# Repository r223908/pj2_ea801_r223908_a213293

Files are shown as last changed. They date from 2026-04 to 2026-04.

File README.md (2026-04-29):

### EA801 - PROJETO 2

### Câmbio CVT Físico com BitDogLab V7

**Autores:** 
- Raul Galdino Tancredo (RA: 223908 / [@r223908](https://github.com/r223908))
- Arthur Lucas Da Silva Nogueira (RA: 213293 / [@arthurnog](https://github.com/arthurnog)))

**Professor:** Eric Rohmer

* **Proposta de Projeto**: [Proposta em G-Docs](https://docs.google.com/document/d/18PMYSmtTR0OQQLU4SV4fV71K-Bi9EbMdW6YyoQtnZmc/edit?usp=sharing) (acesso "Comentador" para UNICAMP)
* **Relatório de projeto**: [Relatório em G-Docs](https://docs.google.com/document/d/1z_JGgpvWlYswWX_sQGRnS61v9bXmHXGZWmitXccoX50/edit?usp=sharing) (acesso "Comentador" para UNICAMP)
* **Demonstração do projeto no YouTube**: [Vídeo](https://youtu.be/2NB8YhYpBq8)

---
## ⚙️ DESCRIÇÃO DO SISTEMA (v1)
O sistema desenvolvido consiste na implementação de uma bancada de testes para um **Câmbio de Transmissão Continuamente Variável (CVT)** simulado, controlado remotamente via interface sem fio. O projeto utiliza a plataforma BitDogLab V7 como unidade central de processamento, integrando comunicação serial, controle de potência e telemetria.

O controle é dividido em dois eixos de atuação:
1. Eixo motor: Um motor de corrente contínua (DC), simulando a rotação do motor primário, controlado via PWM mas com a rotação travada em 100%.
2. Atuador do câmbio: Um segundo motor acoplado a um sistema de fuso (atuador linear), responsável por alterar a posição física da correia do câmbio CVT.

A interface homem-máquina (IHM) é realizada de forma remota através de um módulo Bluetooth (conectado à interface UART da placa) com a integração de um aplicativo no celular. O display OLED da placa é utilizado para exibir a telemetria em tempo real.

<figure align="center">
    <figcaption><i>Figura 1: Diagrama de blocos do projeto.</i></figcaption>
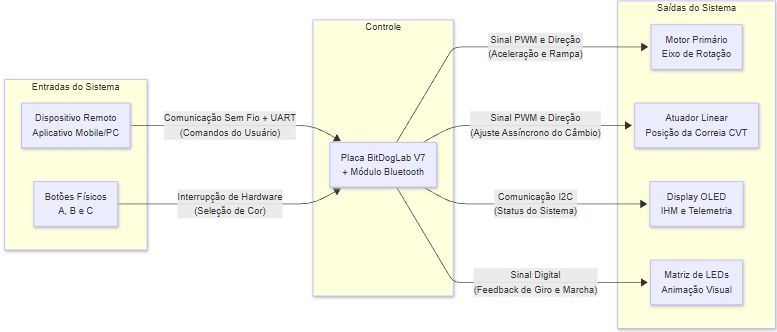
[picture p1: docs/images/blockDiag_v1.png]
Diagrama de blocos do projeto
    
    </br>
</figure>

<figure align="center">
    <figcaption><i>Figura 2: Referência de projeto feito em LEGO.</i></figcaption>
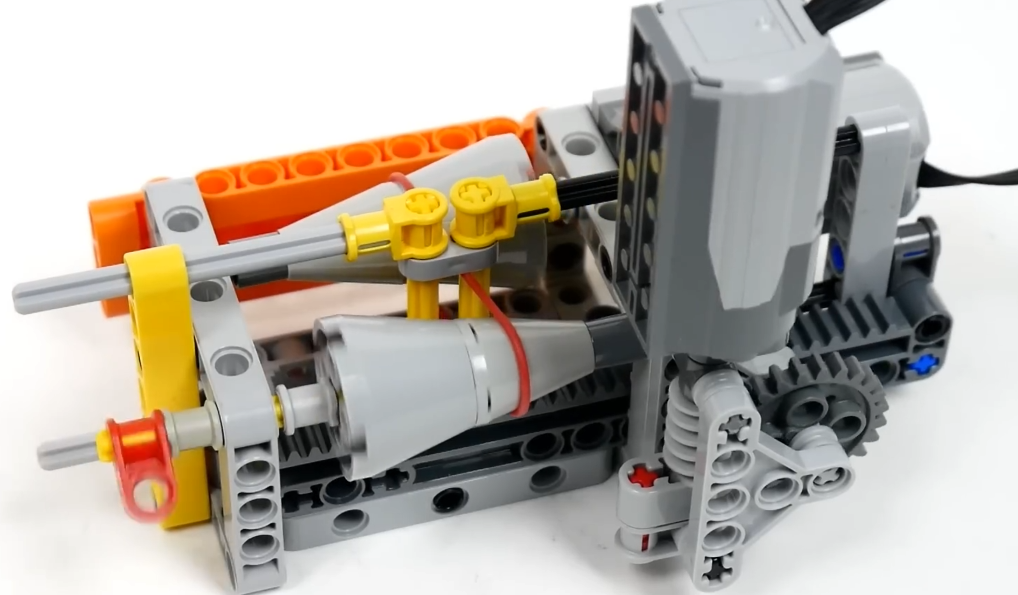
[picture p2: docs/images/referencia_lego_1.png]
Referência LEGO
    
</figure>

<figure align="center">
    <figcaption><i>Figura 3: Projeto em CAD 3D.</i></figcaption>
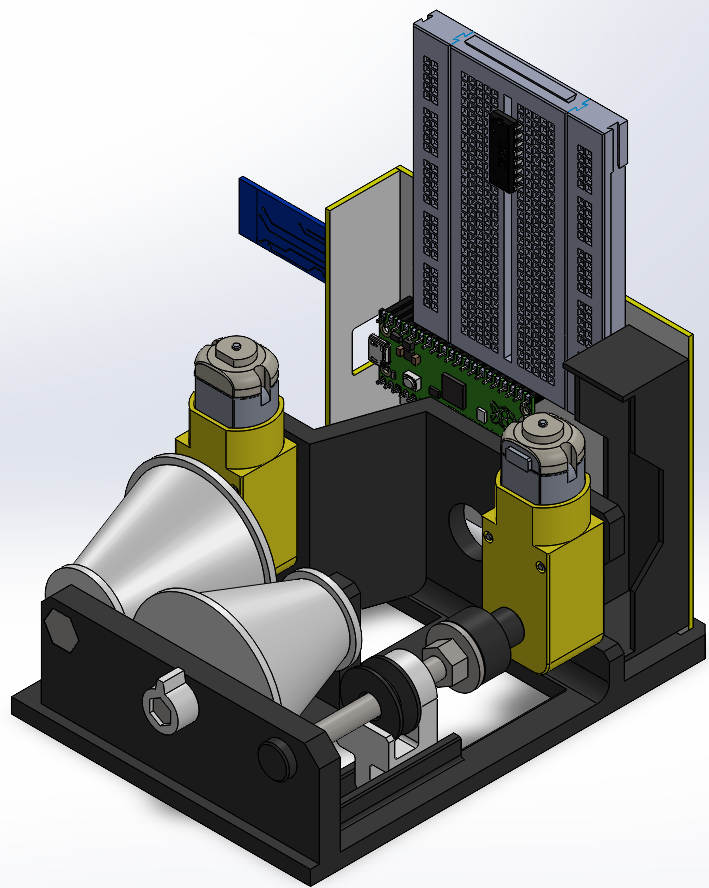
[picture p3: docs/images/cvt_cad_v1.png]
    
</figure>

<figure align="center">
    <figcaption><i>Figura 4: Equipamento testado e montado.</i></figcaption>
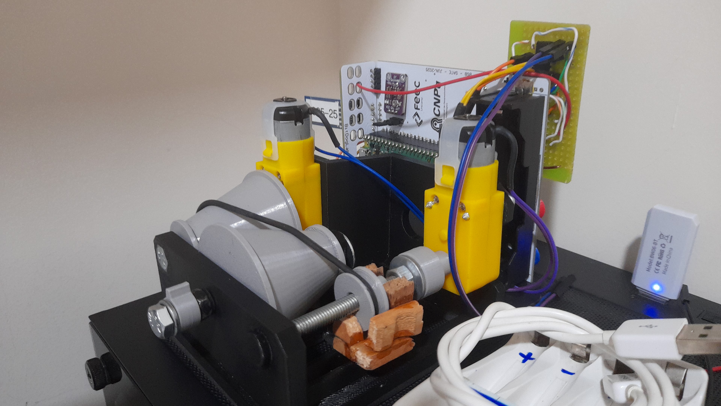
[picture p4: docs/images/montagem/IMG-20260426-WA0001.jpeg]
    
</figure>

---
## ❗REQUISITOS
- 1x BitDogLab V7.
- 2x Ponte H L293D (CI) para ambos os motores.
- 1x Protoboard 400 pinos ou fazer toda a ligação na placa de fenolite com solda.
- Jumpers M-M e M-F.
- 1x Adaptador de 4 pilhas AA (6 Vcc para os motores e alimentação da placa).
- 4x pilhas AA (1,5 Vcc).
- Cabo micro USB (usar apenas para passar a programação, com as pilhas desconectadas).
- Módulo Bluetooth HC05.
- Anel o-ring ou elástico.
- Parafusos para montagem (alguns precisam ser colados na base)
    - 2x Parafuso ISO 4017 M4x20 (Eixos do cone de saída)
    - 1x Parafuso ISO 4017 M6x15 (Contra-eixo do cone principal)
    - 1x Parafuso ISO 4017 M6x60 (fuso do CVT)
    - 2x Porca ISO 4032 M6 (Espaçador no fuso do CVT e guia da polia)
    - 1x Arruela ISO 7093 Ø6 (Espaçador no fuso do CVT)
    - 4x Parafuso autoatarrachante 9/64"x1" (ou 1/8"x1" - Ø x Comprimento)
- Peças impressas em 3D
- Ambiente de desenvolvimento configurado para MicroPython.

---
## 🔧CONFIGURAÇÕES
- BitDogLab V7: Transferir os arquivos **main.py**, **setup.py** e **ssd1306.py** para a placa via USB.
- Ligação das pontes H e motores conforme **/docs/images/schematic.png**
- Módulo Bluetooth HC05 configurado em AT Mode usando **hc05_atMode_config.py**

---
## 📚 REFERÊNCIAS
1. Repositório BitDogLab V7: [Repositório no GitHub](https://gitlab.unicamp.br/fabiano/bitdoglab-v7)
2. Banco de Informação de Hardware: [BitDogLabV7_BIH](https://docs.google.com/document/d/13-68OqiU7ISE8U2KPRUXT2ISeBl3WPhXjGDFH52eWlU/edit?tab=t.0)
3. LEGO Continuous Variable Transmission (CVT) V3 [Link YouTube](https://www.youtube.com/watch?v=sa60egMprYc)
4. LEGO Simple CVT (Continuously Variable Transmission) [Link YouTube](https://www.youtube.com/watch?v=1y5fQr0dDVg)

---
## 📄LICENÇA
* Ver o arquivo `LICENSE`.

---
## 📂 ESTRUTURA DO PROJETO
``` text
├── .vscode/                        → Listagens das config. e bibliotecas
├── docs/                           → Documentação do projeto
│   ├── CAD_files/                  → Arquivos .stl e PDF_3D da montagem
│   ├── datasheets/                 → Folhas de dados dos equipamentos utilizados
│   ├── images/                     → Imagens para relatórios e referências
│   ├── kicad_project/              → Projeto KiCad para a plaquinha shield
│   ├── mermaid_files/              → arquivos para gerar os diagramas de bloco e gantt
│   ├── video/                      → Vídeo original
│   └── (...)                       → Proposta e relatório
├── libs/                           
│   └── (...)                       → Bibliotecas e arquivos de configuração
├── src/                            
│   └── main.py                     → Código-fonte
├── .micropico                      → Arquivo necessário para a extensão Pi PICO no VSCODE
├── LICENSE                         → Licença de uso do código
└── README.md                       → Resumo e estrutura do projeto
```

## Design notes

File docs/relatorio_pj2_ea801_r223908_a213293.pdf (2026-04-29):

## UNICAMP - Universidade Estadual de Campinas

### FEEC - Faculdade de Engenharia Elétrica e de Computação

Câmbio CVT Físico com BitDogLab V7 RELATÓRIO DE PROJETO

Link deste documento (acesso Comentador para UNICAMP): Link (https://docs.google.com/document/d/1z_JGgpvWlYswWX_sQGRnS61v9bXmHXGZWmitXccoX50/edit?usp=sharing) Repositório no GitHub (https://github.com/r223908/pj2_ea801_r223908_a213293)
Vídeo de demonstração (https://youtu.be/2NB8YhYpBq8)
Arthur Lucas Da Silva Nogueira | RA: 213293
Raul Galdino Tancredo | RA: 223908

Prof. Eric Rohmer

Campinas
2026

### 1. Descrição do Sistema

O sistema desenvolvido consiste na implementação de um Câmbio de Transmissão Continuamente Variável (CVT) simulado e controlado remotamente via interface sem fio. O projeto utiliza a plataforma BitDogLab V7 como unidade central de processamento, integrando comunicação serial, controle de potência e telemetria. Utilizando uma ponte H L293D, o controle dos motores é dividido em dois eixos de atuação:
1. Eixo motor: motor de corrente contínua (DC) responsável pela força motriz principal, conectado ao cone principal.
2. Atuador do câmbio: motor de corrente contínua acoplado a um sistema de fuso (atuador linear), responsável por alterar a posição física da correia do câmbio CVT. No sistema de fuso, há a polia (que tem o anel o-ring/elástico girando livremente) e a guia, que faz com que o movimento de rotação do fuso se transforme em movimento linear.

A interface homem-máquina (IHM) é realizada de forma remota através de um módulo Bluetooth (conectado à interface UART da placa) com a integração de um aplicativo no celular (“Arduino Bluetooth Control” na Play Store do Google). O display OLED da placa é utilizado para exibir a telemetria em tempo real.

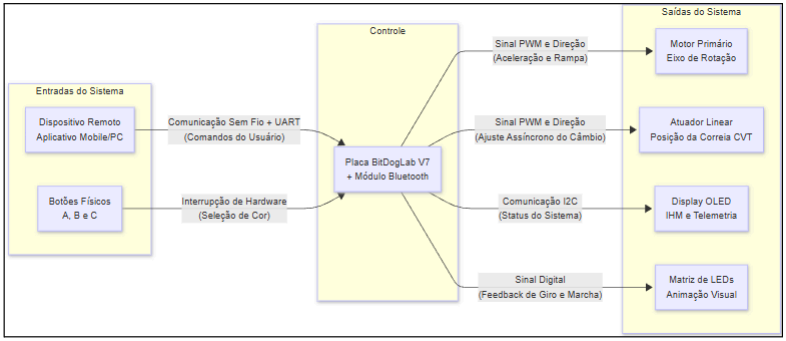
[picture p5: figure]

Figura 1 - Arquitetura do sistema.

Python

### 2. Código fonte

- Configuração do módulo Bluetooth HC-05: /libs/hc05_atMode_config.py (https://github.com/r223908/pj2_ea801_r223908_a213293/blob/main/libs/hc05_atMode_config.py)

"""
Como usar:
1. Segurar botão da placa HC-05 (ao ligar a BitDogLab, o módulo vai piscar os LEDs a cada 2 segundos).
2. Inserir o cabo USB na entrada da BitDogLab.
3. No VSCode, selecionar este .py na árvore usar a opção "Run current file on Pico"
4. Testar interface com o comando "AT" --> Deve aparecer um "OK" onde estava o "AT".
5. Configurar usuário da placa:
a. AT+NAME=.... | --> digitar o nome do módulo; e.g.: AT+NAME=EA801_CVT
b. AT+PSWD=xxxx | --> senha de 4 digitos = xxxx
c. AT+CMODE=1 | --> para se conectar com qualquer dispositivo através da
senha
6. Desligar a placa e realizar pareamento.
A. Para mais comandos, ver /docs/datasheets/HC-05_ATCommandSet.pdf """

import machine
import sys
import uselect
import utime

# Configura a UART0 nos pinos 0 (TX) e 1 (RX) - Conector J2

# O baud rate de 38400 é o padrão de fábrica para o modo AT do HC-05

uart = machine.UART(0, baudrate=38400, tx=machine.Pin(0), rx=machine.Pin(1))

print("==================================")
print(" | Terminal AT para HC-05 | ")
print("==================================")
print("Digite 'AT' e pressione Enter.")
print("A resposta deve ser 'OK'.") print("==================================")

# Configura a entrada do teclado (terminal USB) para não bloquear o código teclado = uselect.poll()

teclado.register(sys.stdin, uselect.POLLIN)

# Envia um "AT" inicial de teste (igual ao seu código C++)

Python

uart.write('AT\r\n')

while True:
# 1. Se chegou algo do HC-05, imprime no terminal do PC

if uart.any():
resposta = uart.read()
if resposta is not None: | # sem isso vai aparecer um erro no decode
abaixo
try:
print(resposta.decode('utf-8'), end='')
except UnicodeError:
print(resposta) # Imprime cru se houver lixo na serial

# 2. Se digitar algo no terminal do PC, 05envia para o HC-

if teclado.poll(0):
comando = sys.stdin.readline().strip() # Lê o que foi digitado
if comando:
# O HC-05 exige que os comandos AT terminem com Carriage Return e Line Feed (\r\n)

uart.write(comando + '\r\n')

utime.sleep(0.01) # Pequena pausa para não sobrecarregar o processador

- Mapeamento de comandos Bluetooth: /libs/bluetooth_mapping.py (https://github.com/r223908/pj2_ea801_r223908_a213293/blob/main/libs/bluetooth_mapping.py)

"""
1. Arquivo de uso geral para mapear o que chega de informação na UART com o módulo bluetooth.
2. Utilizado para reconhecer os comandos e configurar o setup.py deste projeto.
3. O que a placa receber será exibido no Terminal do VSCode.
"""

import machine
import utime

# Inicializa a UART0 para o Bluetooth (Pinos do Conector J2)

# Baud rate 9600 é o padrão para comunicação (modo transparente)

bluetooth = machine.UART(0, baudrate=9600, tx=machine.Pin(0), rx=machine.Pin(1))

# Configura o LED Azul da placa (GPIO 12) para feedback visual

# O BIH diz que é cátodo comum, então '1' liga e '0' desliga

led_azul = machine.Pin(12, machine.Pin.OUT)
led_azul.value(0) # Inicia desligado

Python

print("=======================================")
print(" | Monitor Bluetooth - Projeto CVT | ")
print("=======================================") print("Aguardando conexão e comandos do celular...")

while True:
# Verifica se há dados no buffer do Bluetooth if bluetooth.any():

| # Lê os dados brutos recebidos dados_brutos = bluetooth.read()
| try:
# Tenta decodificar de bytes para texto (String)

# O .strip() remove espaços em branco e quebras de linha (\r, \n) das pontas

comando = dados_brutos.decode('utf-8').strip() # type: ignore

# Só imprime se realmente tiver algo após o strip

| if comando:
print(f"Comando recebido em Texto: '{comando}'")

# Envia um "eco" de volta para o celular (aparece na tela do app) bluetooth.write(f"Placa recebeu: {comando}\n")

| # Pisca o LED Azul rapidamente led_azul.value(1) utime.sleep(0.1) led_azul.value(0)
| except UnicodeError:
# Se o aplicativo do celular mandar dados hexadecimais puros

# (comum em apps de controle tipo "joystick"), a decodificação de texto falha.

# Nesse caso, imprimimos os bytes puros para você poder mapear. print(f"Dados recebidos em Bytes (Hex): {dados_brutos}")

# Pausa curta para não travar a CPU no loop infinito utime.sleep(0.05)

- Setup do projeto: /libs/setup.py (https://github.com/r223908/pj2_ea801_r223908_a213293/blob/main/libs/setup.py)

"""
arquivo de importação de bibliotecas, configuração de interfaces e variáveis """

from machine import Pin, ADC, I2C, PWM import neopixel, utime, machine import ssd1306

# 1. Variáveis Globais e Cores corVermelha = (20, 0, 0)

corAzul = (0, 0, 20)
corVerde = (0, 20, 0)
cor_travada = corVermelha # Motor começa vermelho ultimo_tempo_btn = 0
ultimo_tempo_pisca = utime.ticks_ms() indice_frame = 0

# 2. Variáveis de Controle do Motor Virtual

CENTRO_JOYSTICK = 32768
ZONA_MORTA = 4000
MAX_LEDS_POR_SEGUNDO = 100 # Ajuste a velocidade máxima aqui

# 3. Configuração dos Botões (A, B e C)

botao_a = Pin(5, Pin.IN, Pin.PULL_UP)
botao_b = Pin(6, Pin.IN, Pin.PULL_UP)
botao_c = Pin(10, Pin.IN, Pin.PULL_UP)

# 4. Configuração do Joystick

joystick_x = ADC(Pin(27))
joystick_y = ADC(Pin(26))
joystick_sw = Pin(22, Pin.IN, Pin.PULL_UP)

# 5. Configuração do Display OLED (SSD1306)

# Usando os pinos I2C0 da BitDogLab V7 (SDA=2, SCL=3) i2c = I2C(1, scl=Pin(3), sda=Pin(2), freq=400000) display = ssd1306.SSD1306_I2C(128, 64, i2c, addr=0x3C) display.fill(0)

display.show()
ATT_DISPLAY_MS = 100

# 6. Configuração da Matriz de LEDs NUM_LEDS = 25

np = neopixel.NeoPixel(Pin(7), NUM_LEDS)
LED_MEIO = 12
# Buffer circular da animação do motor

FRAMES_MOTOR = [[14, 13], [15, 16], [16, 24], [16, 23], [17, 22], [18, 21], [18, 20], [18, 19], [10, 11], [8, 9],

[0, 8], [1, 8], [2, 7], [3, 6], [4, 6], [5, 6] ]

# 7. Configuração dos controles de Motor (Ponte H) e PWM da placa

# IMPORTANTE: GPIO 0 e 1 são do Bluetooth. Vamos usar os pinos livres do conector IDC.

# Motor Principal (Eixo)

Mprincipal_DIR1 = Pin(16, Pin.OUT)
Mprincipal_DIR2 = Pin(17, Pin.OUT) Mprincipal_PWM = PWM(Pin(18)) Mprincipal_PWM.freq(1000)
Mprincipal_PWM.duty_u16(0) TEMPO_RAMPA_MS = 1000
# Motor Câmbio (Atuador CVT) Mcambio_DIR1 = Pin(19, Pin.OUT) Mcambio_DIR2 = Pin(8, Pin.OUT) Mcambio_PWM = PWM(Pin(9))

Mcambio_PWM.freq(1000)
Mcambio_PWM.duty_u16(0)
TEMPO_PASSO_CVT_MS = 2000 # 2000 ms = 2 segundos

# 8. Configura o LED Azul da placa (GPIO 12) para feedback visual led_azul = machine.Pin(12, machine.Pin.OUT)

led_azul.value(0) # Inicia desligado

# 9. Inicializa a UART0 para o Bluetooth (Pinos do Conector J2)

bluetooth = machine.UART(0, baudrate=9600, tx=machine.Pin(0), rx=machine.Pin(1)) status_bt = machine.Pin(4, machine.Pin.IN) # Pino que vai ler o pino 'STATE' do módulo Bluetooth

# 10. Mapeamento das entradas bluetooth

outButtonDir = '0'
frontDir = 'F'
backDir = 'B'
rightDir = 'R'
leftDir = 'L'
triangleDir = 'T'
circleDir = 'C'
squareDir = 'S'
crossDir = 'X'
startDir = 'A'
pauseDir = 'P'

Python

- Arquivo principal: /src/main.py (https://github.com/r223908/pj2_ea801_r223908_a213293/blob/main/src/main.py)

from setup import *

# ========================================== # FUNÇÕES DE HARDWARE (MOTORES E TELA)

# ==========================================

# Lida com as informações do display OLED

def printOled(velocidade, direcao, posicao_cvt, bt_conectado): texto_sentido = "Horario" if direcao == 1 else "Anti-Hor." texto_sentido = "Parado" if velocidade == 0 else texto_sentido texto_bt = "ON" if bt_conectado == 1 else "OFF" display.fill(0)
display.text("Cambio CVT", 20, 0)
display.text("-" * 16, 0, 10) display.text(f"Motor: {texto_sentido}", 0, 25) display.text(f"Pos. CVT: {posicao_cvt}%", 0, 40)
display.text(f"Bluetooth: {texto_bt}", 0, 55)
display.show()

#controle do motor principal, lidando com a velocidade (mantida em 100%) e sentido de giro

def controlar_motor_principal(velocidade_percentual, direcao, fazer_rampa=False): # verificação se recebeu o comando para inverter o sentido do motor ou parar # nos dois casos tem rampa de variação de velocidade para não ter um solavanco nos componentes mecânicos
if fazer_rampa and velocidade_percentual > 0:
passos = 10
tempo_por_passo = (TEMPO_RAMPA_MS / 2000) / passos passo_pwm = max(1, velocidade_percentual // passos) for v in range(velocidade_percentual, -1, -passo_pwm): Mprincipal_PWM.duty_u16(int((v / 100) * 65535)) utime.sleep(tempo_por_passo) Mprincipal_DIR1.value(0)
Mprincipal_DIR2.value(0)
Mprincipal_PWM.duty_u16(0)
utime.sleep(0.05)
if direcao == 1: | # a mudança de direção pode ser feita na
inversão dos fios de alimentação do motor Mprincipal_DIR1.value(1)
Mprincipal_DIR2.value(0)
else:
Mprincipal_DIR1.value(0)
Mprincipal_DIR2.value(1)
for v in range(0, velocidade_percentual + 1, passo_pwm):

Mprincipal_PWM.duty_u16(int((v / 100) * 65535)) utime.sleep(tempo_por_passo) Mprincipal_PWM.duty_u16(int((velocidade_percentual / 100) * 65535))
else: | # controle normal, apenas ocorre se recebe algum comando via
Bluetooth
if velocidade_percentual > 0:
| if direcao == 1: Mprincipal_DIR1.value(1) Mprincipal_DIR2.value(0)

else:
| Mprincipal_DIR1.value(0) Mprincipal_DIR2.value(1)

else:
| Mprincipal_DIR1.value(0) Mprincipal_DIR2.value(0)

Mprincipal_PWM.duty_u16(int((velocidade_percentual / 100) * 65535))

# movimentação do câmbio, dependendo do sentido que ele precisar girar # velocidade também sempre em 100%

def iniciar_movimento_cvt(direcao):
if direcao == 1:
Mcambio_DIR1.value(1)
Mcambio_DIR2.value(0)
elif direcao == -1:
Mcambio_DIR1.value(0)
Mcambio_DIR2.value(1)
else:
return
Mcambio_PWM.duty_u16(65535)

# ========================================== # Função de Interrupção dos Botões

# ========================================== def trata_interrupcao_botao(pino):

global cor_travada, ultimo_tempo_btn
tempo_atual = utime.ticks_ms()
if utime.ticks_diff(tempo_atual, ultimo_tempo_btn) > 200: if pino == botao_a:
| cor_travada = corVermelha
elif pino == botao_b:
| cor_travada = corAzul
elif pino == botao_c:
| cor_travada = corVerde
ultimo_tempo_btn = tempo_atual botao_a.irq(trigger=Pin.IRQ_FALLING, handler=trata_interrupcao_botao) botao_b.irq(trigger=Pin.IRQ_FALLING, handler=trata_interrupcao_botao) botao_c.irq(trigger=Pin.IRQ_FALLING, handler=trata_interrupcao_botao)

# ==========================================

# INICIALIZAÇÃO E LOOP PRINCIPAL

# ==========================================

ultimo_tempo_pisca = utime.ticks_ms() ultimo_tempo_oled = utime.ticks_ms()

# inicializacao dos motores velocidade_atual = 0

direcao_motor = 1
posicao_cvt = 0

# VARIÁVEIS PARA O CVT ASSÍNCRONO cvt_em_movimento = False

ultimo_tempo_cvt = 0

# desliga a matriz de LEDs

for i in range(NUM_LEDS):
np[i] = (0, 0, 0)
np.write()

print("Aguardando comandos Bluetooth...")

while True:
tempo_atual = utime.ticks_ms()

# 1. ATUALIZAÇÃO DO DISPLAY OLED

if utime.ticks_diff(tempo_atual, ultimo_tempo_oled) >= ATT_DISPLAY_MS: estado_conexao = status_bt.value()
if estado_conexao == 0 and velocidade_atual > 0:
passos = 10
tempo_por_passo = (TEMPO_RAMPA_MS / 2000) / passos passo_pwm = max(1, velocidade_atual // passos)
for v in range(velocidade_atual, -1, -passo_pwm): Mprincipal_PWM.duty_u16(int((v / 100) * 65535)) utime.sleep(tempo_por_passo)
velocidade_atual = 0
controlar_motor_principal(0, direcao_motor) printOled(velocidade_atual, direcao_motor, posicao_cvt, estado_conexao) ultimo_tempo_oled = tempo_atual

# 2. LEITURA DE COMANDOS BLUETOOTH

if bluetooth.any():
try:
dados_brutos = bluetooth.read()
if dados_brutos is not None:
comando = dados_brutos.decode('utf-8').strip().upper()

if comando:
led_azul.value(1)
if comando == startDir: | # ligar motor principal
velocidade_atual = 100
controlar_motor_principal(velocidade_atual, direcao_motor)
elif comando == frontDir: | # sentido horário
deve_fazer_rampa = (direcao_motor == -1 and velocidade_atual > 0)
direcao_motor = 1
controlar_motor_principal(velocidade_atual, direcao_motor, deve_fazer_rampa)
elif comando == backDir: | # sentido anti-horário
deve_fazer_rampa = (direcao_motor == 1 and velocidade_atual > 0)
direcao_motor = -1
controlar_motor_principal(velocidade_atual, direcao_motor, deve_fazer_rampa)

elif comando == triangleDir: # sobe marcha; motor CVT
# Adicionada a regra: "not cvt_em_movimento" para evitar acúmulo de comandos

if posicao_cvt < 100 and not cvt_em_movimento: iniciar_movimento_cvt(1)
cvt_em_movimento = True
ultimo_tempo_cvt = tempo_atual # Marca a hora que ligou
posicao_cvt = min(100, posicao_cvt + 10)
elif comando == crossDir: | # desce marcha; motor CVT
if posicao_cvt > 0 and not cvt_em_movimento: iniciar_movimento_cvt(-1)
cvt_em_movimento = True
ultimo_tempo_cvt = tempo_atual # Marca a hora que ligou
posicao_cvt = max(0, posicao_cvt - 10)

elif comando == pauseDir: | # para o motor principal
velocidade_atual = 0
controlar_motor_principal(0, direcao_motor)
# Parada de emergência para o Câmbio também! Mcambio_DIR1.value(0)

Mcambio_DIR2.value(0)
Mcambio_PWM.duty_u16(0)
cvt_em_movimento = False

led_azul.value(0)
except UnicodeError:
pass

# 3. VERIFICADOR ASSÍNCRONO DO MOTOR CVT

# Fica verificando se o tempo do motor do câmbio já deu

if cvt_em_movimento:
if utime.ticks_diff(tempo_atual, ultimo_tempo_cvt) >= TEMPO_PASSO_CVT_MS: # O tempo do passo (ex: 2s) acabou! Desliga o motor do CVT. Mcambio_DIR1.value(0)
Mcambio_DIR2.value(0)
Mcambio_PWM.duty_u16(0)
cvt_em_movimento = False

# 4. ANIMAÇÃO DA MATRIZ DE LEDS PARA REPLICAR O SENTIDO DE GIRO DO MOTOR PRINCIPAL

np.fill((0, 0, 0))
if posicao_cvt == 0 or velocidade_atual == 0:
np[LED_MEIO] = cor_travada
else:
leds_por_segundo = (posicao_cvt / 100) * MAX_LEDS_POR_SEGUNDO leds_por_segundo = .1 if leds_por_segundo < 0.1 else leds_por_segundo intervalo_ms = int(1000 / leds_por_segundo)

if utime.ticks_diff(tempo_atual, ultimo_tempo_pisca) >= intervalo_ms: if direcao_motor == 1:
indice_frame = (indice_frame + 1) % len(FRAMES_MOTOR) else:
indice_frame = (indice_frame - 1) % len(FRAMES_MOTOR)

ultimo_tempo_pisca = tempo_atual

for led in FRAMES_MOTOR[indice_frame]: np[led] = cor_travada
np.write()

JSON

utime.sleep(0.01)

Para que a pasta /libs/ seja reconhecida ao clonar o repositório, é necessário alterar/criar o arquivo settings.json na pasta .vscode /.vscode/settings.json com a linha "./libs":

{
"python.languageServer": "Pylance", "python.analysis.typeCheckingMode": "basic", "python.analysis.diagnosticSeverityOverrides": { "reportMissingModuleSource": "none"
},
"python.terminal.activateEnvironment": false, "micropico.openOnStart": true, "python.analysis.typeshedPaths": [ "~/.micropico-stubs/included"
],
"python.analysis.extraPaths": [ "~/.micropico-stubs/included", "./libs"
]
}

### 3. Projeto CAD 3D

Com o auxílio de um software de modelagem 3D, foram criadas as peças para impressão 3D dos componentes do projeto: base, cones, polias (de saída e da guia do câmbio), guia e acoplamento do câmbio.
Com os arquivos prontos, é necessário gerar para cada uma das peças um arquivo .stl que é utilizado nas impressoras 3D. Para este projeto, os arquivos podem ser encontrados em:
- Arquivos .stl e PDF 3D: /docs/CAD_files. (https://github.com/r223908/pj2_ea801_r223908_a213293/tree/main/docs/CAD_files)

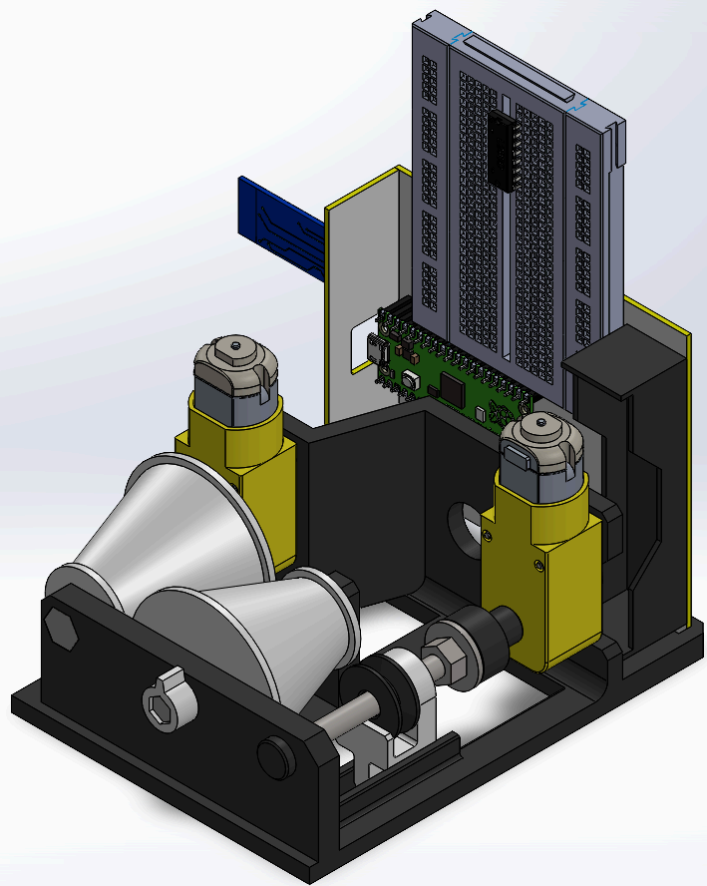
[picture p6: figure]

Figura 2 - Montagem 3D do projeto preliminar.

### 4. Montagem e desvios de projeto

Previamente à manufatura das peças em 3D, realizaram-se os testes de bancada para validar a programação e o acionamento dos motores. Após a validação de ambos os atuadores, o sistema de controle com a ponte H foi consolidado em uma placa de fenolite. O objetivo dessa montagem foi conferir estabilidade física aos componentes elétricos e mitigar o risco de rompimento dos cabos quando o sistema fosse submetido a vibrações.

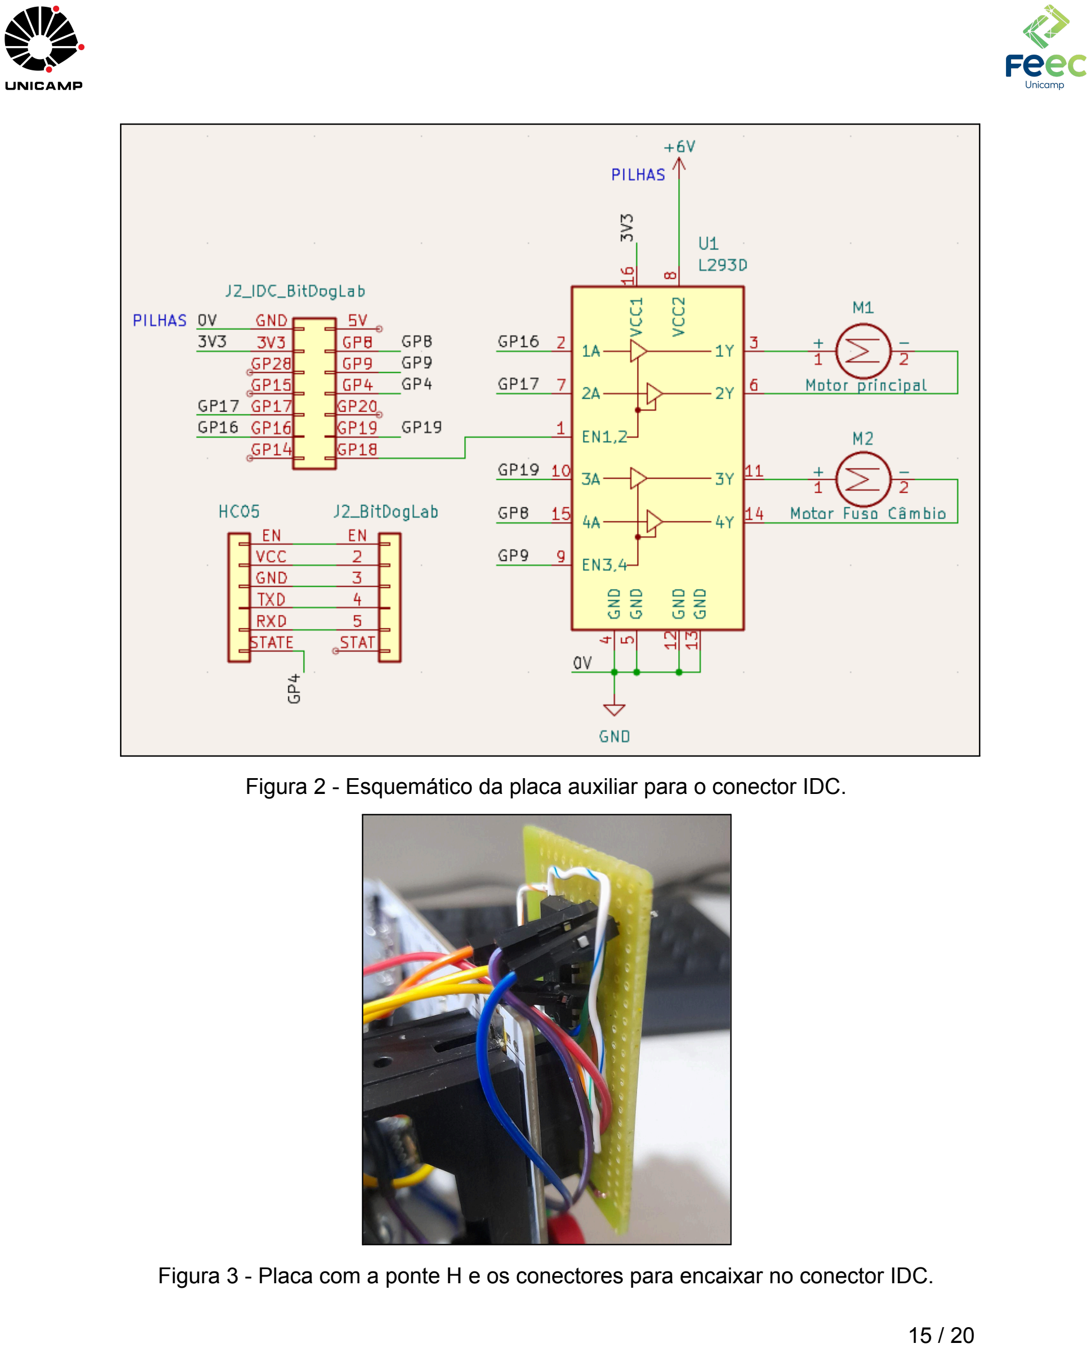
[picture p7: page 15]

Figura 2 - Esquemático da placa auxiliar para o conector IDC.

Figura 3 - Placa com a ponte H e os conectores para encaixar no conector IDC.

Foi adaptado um carregador de pilhas AA/AAA para que ele fosse utilizado como adaptador de 4 pilhas AA para 6 Vcc para alimentação dos motores. Foi feita uma tentativa de alimentação da placa com estes 6V com o auxílio de 2 diodos 1N4007 (gerando 4,6V para o pino 5V do conector IDC), mas as pilhas se provaram insuficientes para a carga da placa e dos dois motores.

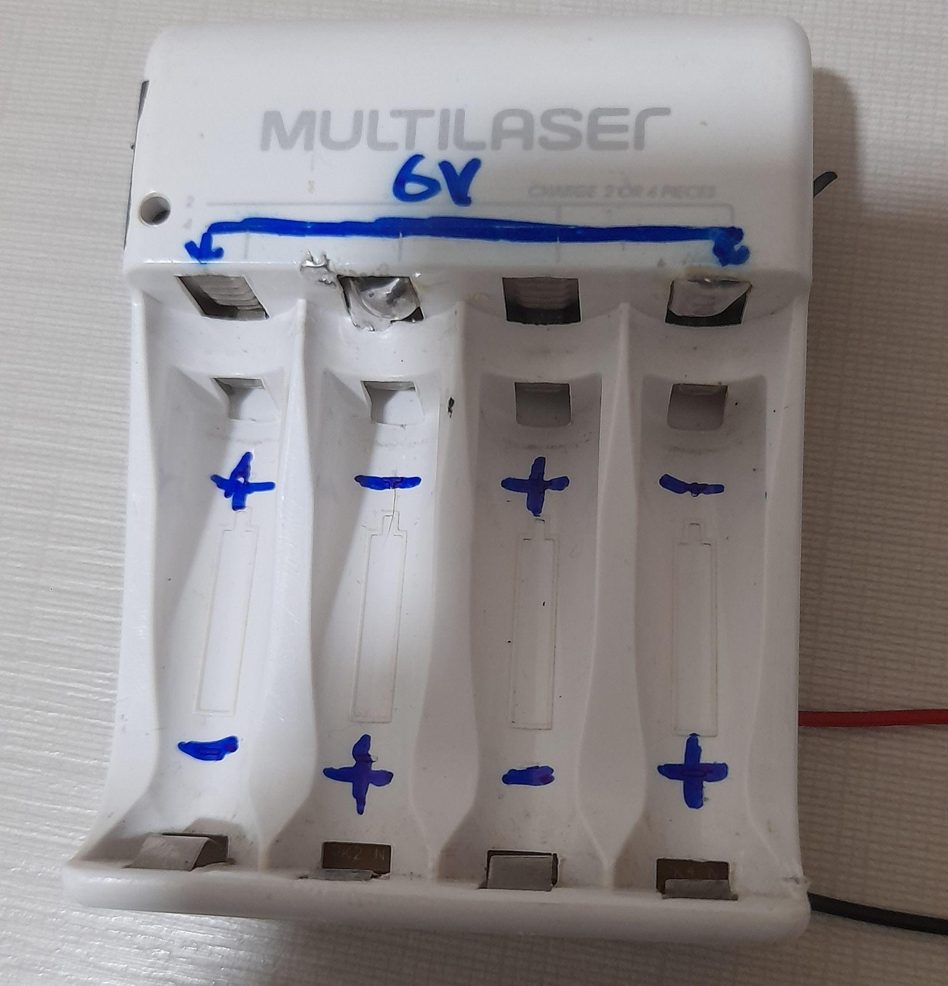
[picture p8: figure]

Figura 4 - Adaptador de pilhas AA para 6 Vcc.

Para a conexão do módulo Bluetooth, a BitDogLab conta com o jumper J2. A única alteração que precisou ser feita é em relação ao pino de estado da conexão bluetooth. Para monitorar se o sistema estava conectado ao celular ou não, foi necessário remover apenas o pino STATE do jumper J2 e colocá-lo na GP4 pois a BitDogLab não possui nenhuma conexão deste pino com alguma entrada da placa.

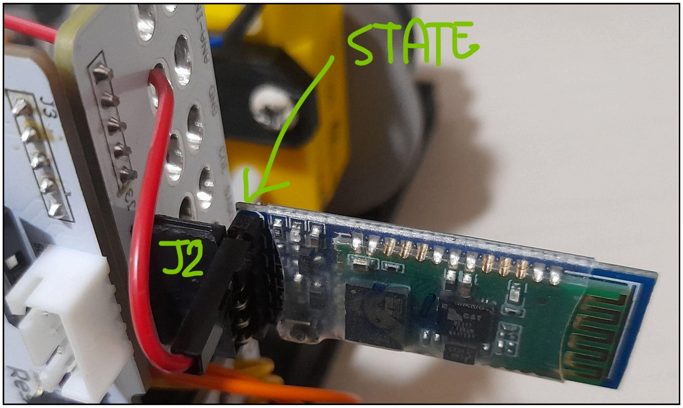
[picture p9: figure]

Figura 5 - Adaptação no módulo HC-05 e jumper J2.

Após a impressão das peças, notou-se que um dos arquivos .stl não foi enviado: a guia da polia do câmbio. Esta peça é responsável por fazer com que uma porca M6 no fuso não gire junto com sua rotação. Assim, o movimento circular realizado pelo fuso é transformado em movimento linear. Para mitigar este problema sem atrasar os testes, foi feito um suporte com prendedores de roupa.

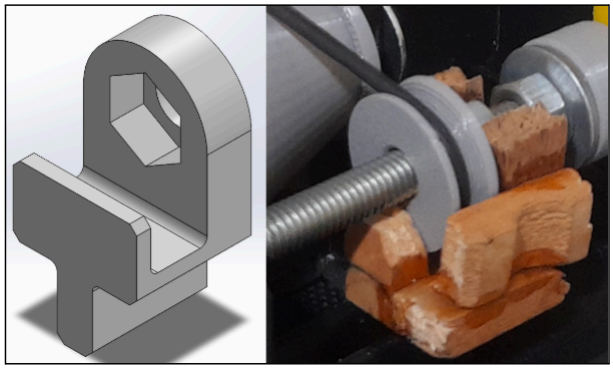
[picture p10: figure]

Figura 6 - Comparativo entre a peça projetada e a peça fabricada para os testes.

### 5. Testes realizados

Os motores foram testados individualmente antes das peças 3D ficarem prontas, validando a lógica de controle do equipamento. O mesmo é válido para a placa que substituiu a protoboard.
Com a confecção das peças em 3D e montagem do sistema, constatou-se que os cones estavam raspando na base e nos parafusos dos eixos. Com as ferramentas adequadas, a peça base foi retrabalhada e os furos centrais dos cones foram aumentados. Com estas alterações, o projeto 3D foi asbuiltado para que numa futura montagem não ocorram os mesmos problemas.
Resolvidos os problemas de interferência das peças, foram feitos alguns testes com o controle dos motores e foi encontrado apenas um problema crítico ao projeto: a guia do câmbio.
Como a guia está em uma extremidade do sistema, o anel o-ring utilizado como “correia” não fica perfeitamente reto ao longo da sua passagem pelos cones. Assim, quanto mais próximo da posição 0%, maior a divergência no tracionamento do cone de saída.

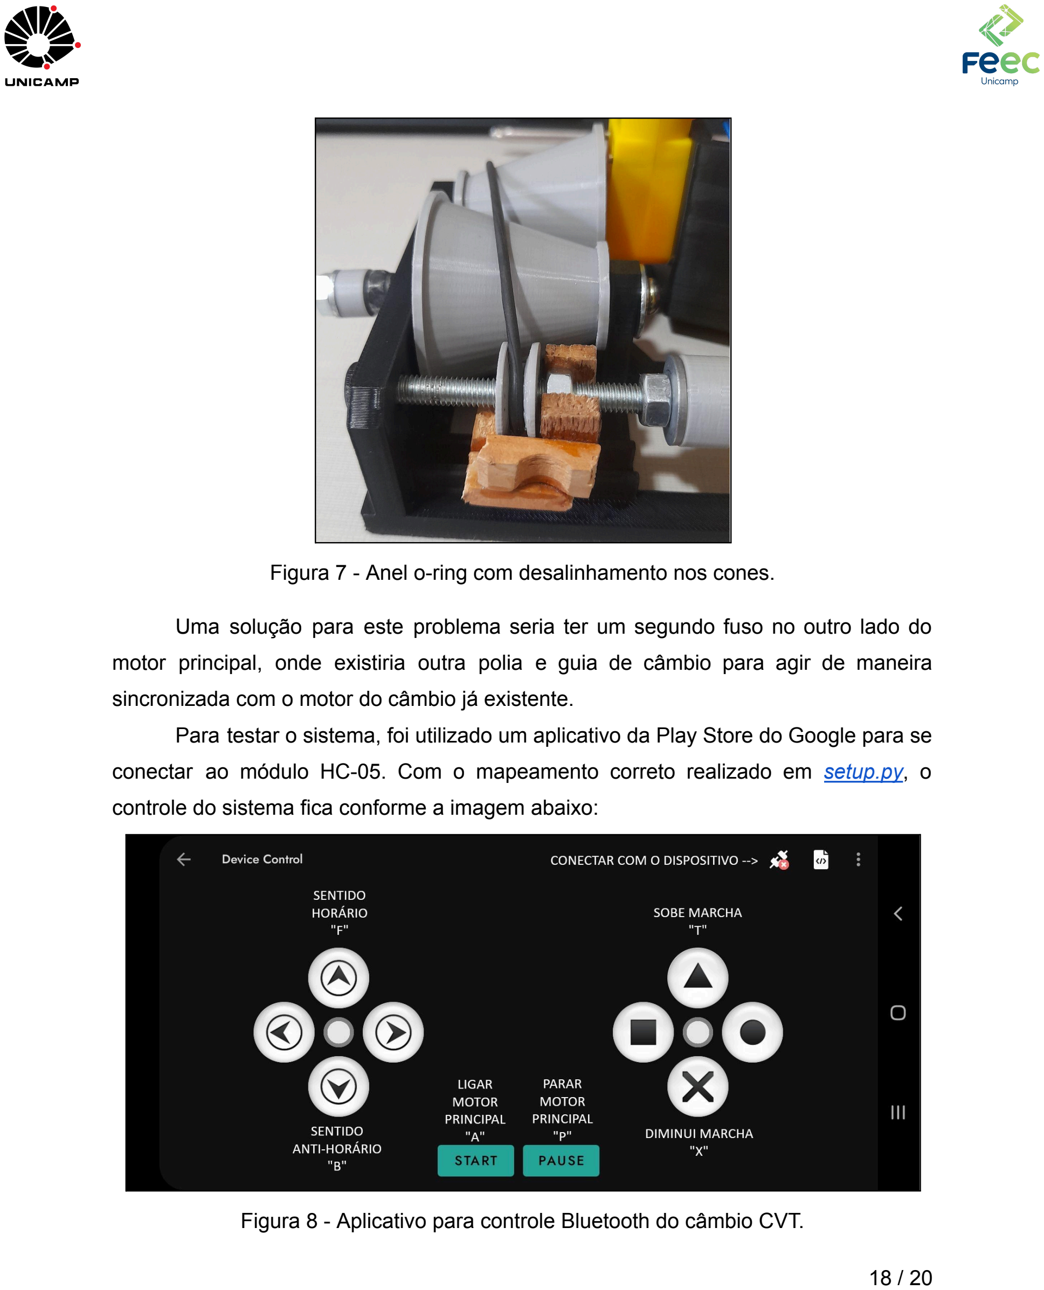
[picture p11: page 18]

Figura 7 - Anel o-ring com desalinhamento nos cones.

Uma solução para este problema seria ter um segundo fuso no outro lado do motor principal, onde existiria outra polia e guia de câmbio para agir de maneira sincronizada com o motor do câmbio já existente.
Para testar o sistema, foi utilizado um aplicativo da Play Store do Google para se conectar ao módulo HC-05. Com o mapeamento correto realizado em setup.py, o controle do sistema fica conforme a imagem abaixo:

Figura 8 - Aplicativo para controle Bluetooth do câmbio CVT.

Após alguns testes, foi constatado a transferência de movimento de maneira satisfatória quando a polia guia do o-ring fica na região central dos cones.

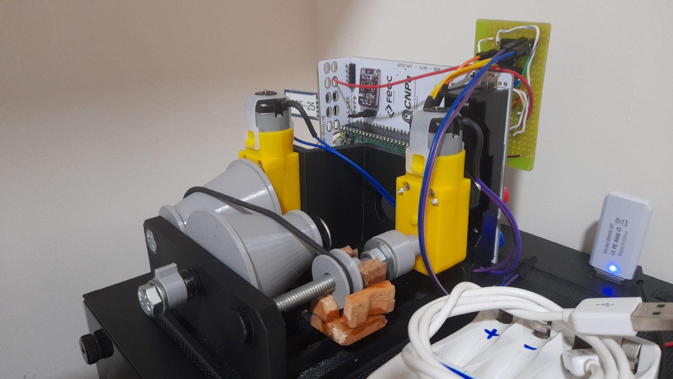
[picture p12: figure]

Figura 9 - Sistema completo.

### 6. Conclusão

O projeto desmontou a viabilidade de desenvolver e controlar um protótipo funcional de um câmbio continuamente variável (CVT) utilizando a BitDogLab e sua interface UART para controle, com o uso de um módulo bluetooth HC-05.
A implementação do controle em malha aberta com operações assíncronas garantiu uma resposta rápida aos comandos remotos via Bluetooth, enquanto o uso de sinais PWM com rampas de aceleração/desaceleração provou-se fundamental para preservar a integridade mecânica dos motores e do sistema de fuso. Além disso, com os feedbacks visuais através do display OLED e matriz de LEDs, o sistema conta com uma IHM (interface homem-máquina) com telemetria clara e em tempo real.
No aspecto mecânico, a conversão do movimento rotacional em linear por meio do sistema de fuso e porca atuou de forma satisfatória para a troca das relações de marcha. Porém, na fase de testes práticos foram encontradas limitações estruturais do protótipo, destacando-se o desalinhamento do anel o-ring (correia).

Em resumo, o projeto atingiu seu objetivo educacional e técnico, consolidando conceitos de sistemas embarcados, cinemática, eletrônica de potência e programação estruturada em um dispositivo mecatrônico de aplicação real.

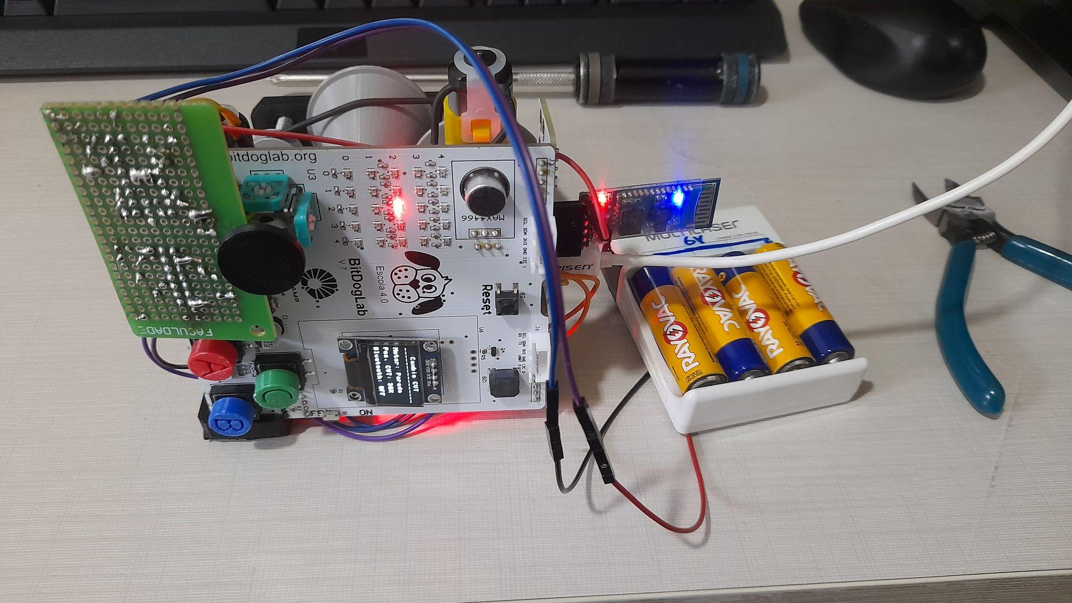
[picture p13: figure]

Figura 10 - Sistema funcionando.

### 7. Referências

- FRUETT, F. BitDogLab V7: repositório oficial. Campinas: Unicamp, 2024. Disponível em: https://gitlab.unicamp.br/fabiano/bitdoglab-v7.
- FRUETT, F. Banco de informações da BitDogLab V7. [S. l.], 2024. Disponível em: https://docs.google.com/document/d/13-68OqiU7ISE8U2KPRUXT2ISeBl3WPhXjGDFH 52eWlU. (https://docs.google.com/document/d/13-68OqiU7ISE8U2KPRUXT2ISeBl3WPhXjGDFH52eWlU)
- r223908; a213293. PJ2 EA801: repositório de desenvolvimento do projeto. GitHub, 2026. Disponível em:https://github.com/r223908/pj2_ea801_r223908_a213293.

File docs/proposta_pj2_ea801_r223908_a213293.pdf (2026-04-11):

## UNICAMP - Universidade Estadual de Campinas

FEEC - Faculdade de Engenharia Elétrica e de Computação

Câmbio CVT Físico com BitDogLab V7 PROPOSTA DE PROJETO

Link deste documento (acesso Comentador para UNICAMP): Link (https://docs.google.com/document/d/18PMYSmtTR0OQQLU4SV4fV71K-Bi9EbMdW6YyoQtnZmc/edit?usp=sharing) Repositório no GitHub (https://github.com/r223908/pj2_ea801_r223908_a213293)

Arthur Lucas Da Silva Nogueira | RA: 213293
Raul Galdino Tancredo | RA: 223908

Prof. Eric Rohmer

Campinas
2026

### 1. Descrição do sistema

O sistema desenvolvido consiste na implementação de uma bancada de testes para um Câmbio de Transmissão Continuamente Variável (CVT) simulado, controlado remotamente via interface sem fio. O projeto utiliza a plataforma BitDogLab V7 como unidade central de processamento, integrando comunicação serial, controle de potência e telemetria.

O controle é dividido em dois eixos de atuação:
- Eixo motor: Um motor de corrente contínua (DC), simulando a rotação do motor primário, controlado via PWM.
- Atuador do câmbio: Um segundo motor acoplado a um sistema de fuso (atuador linear), responsável por alterar a posição física da correia do câmbio CVT.

A interface homem-máquina (IHM) é realizada de forma remota através de um módulo Bluetooth (conectado à interface UART da placa) com a integração de um aplicativo no celular. O display OLED da placa é utilizado para exibir a telemetria em tempo real.

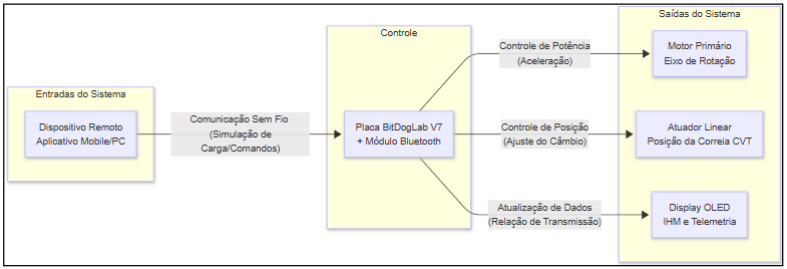
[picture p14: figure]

Figura 1 - Diagrama de blocos do sistema.

Todo o sistema será montado em uma estrutura feita com impressão 3D, de modo que seja uma bancada de testes móveis que precise apenas ser conectada à uma fonte de alimentação no local de instalação. Como referência, foram encontrados alguns projetos feitos em LEGO:

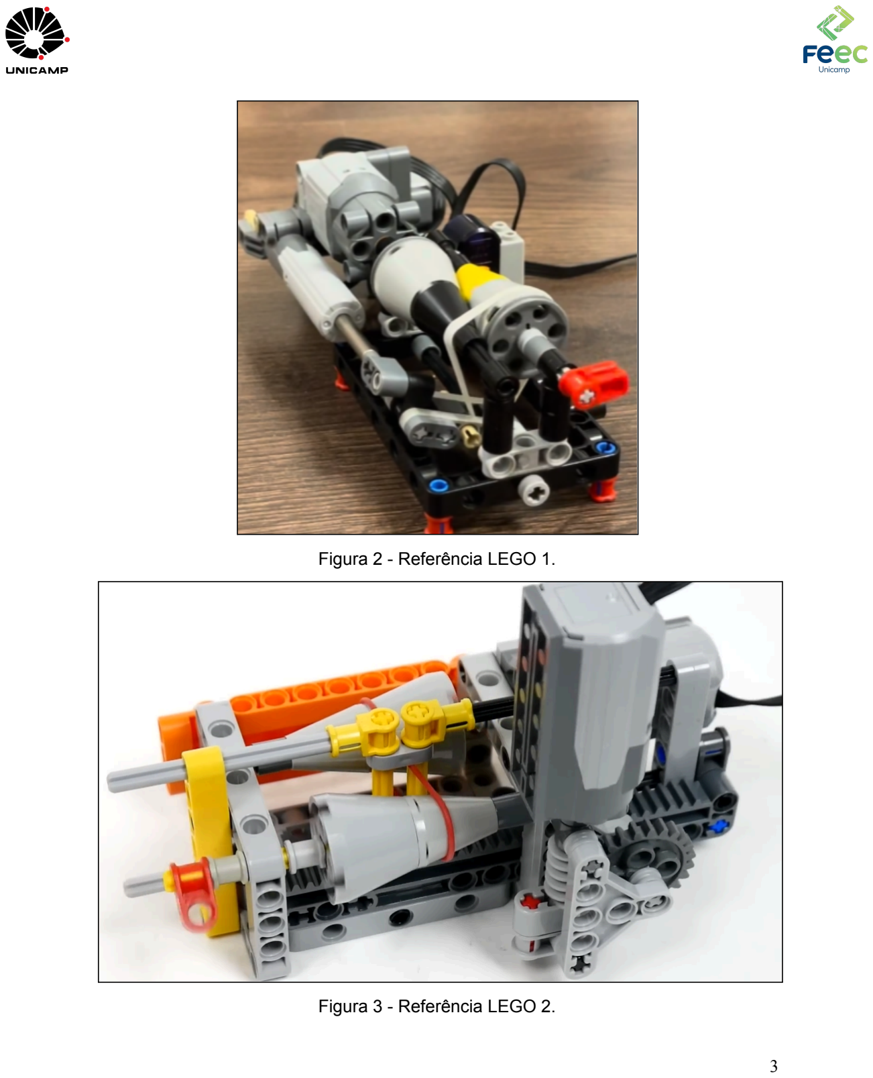
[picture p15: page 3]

Figura 2 - Referência LEGO 1.

Figura 3 - Referência LEGO 2.

### 2. Lista preliminar de peças

- BitDogLab V7.
- Ponte H L293D (CI) para ambos os motores.
- Protoboard 400 pinos.
- Jumpers.
- Fonte regulável.
- Cabo micro USB.
- Ambiente de desenvolvimento configurado para MicroPython.

### 3. Resultados esperados

Ao final deste projeto, espera-se consolidar o desenvolvimento de um protótipo funcional que demonstre excelência tanto em sua execução física quanto lógica. Dessa forma, os resultados pretendidos dividem-se em duas frentes principais.
- Integração eletromecânica: sistema mecânico estruturalmente confiável e estável - escolha adequada de materiais, fixações, motores e organização segura do circuito eletrônico de potência.
- Arquitetura de Software: No âmbito lógico, almeja-se entregar um software embarcado rigorosamente documentado, modular e eficiente.

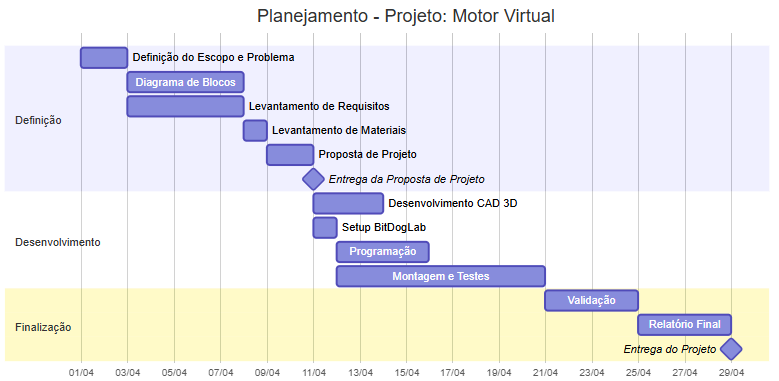
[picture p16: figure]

Figura 4 - Planejamento de projeto.

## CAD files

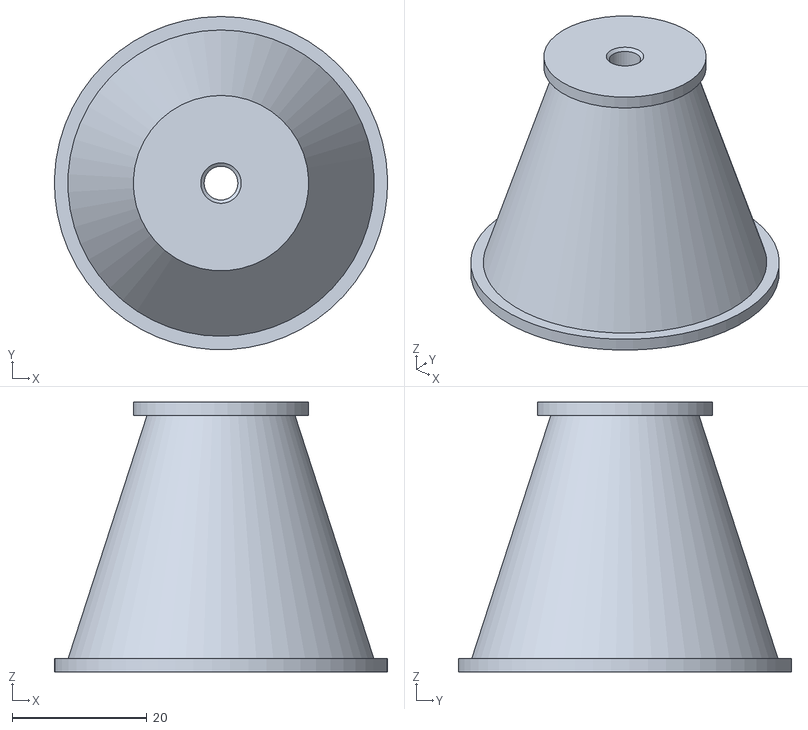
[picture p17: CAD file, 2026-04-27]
docs/CAD_files/3_cone_saida_v2.STL
49.4 x 49.4 x 40.0

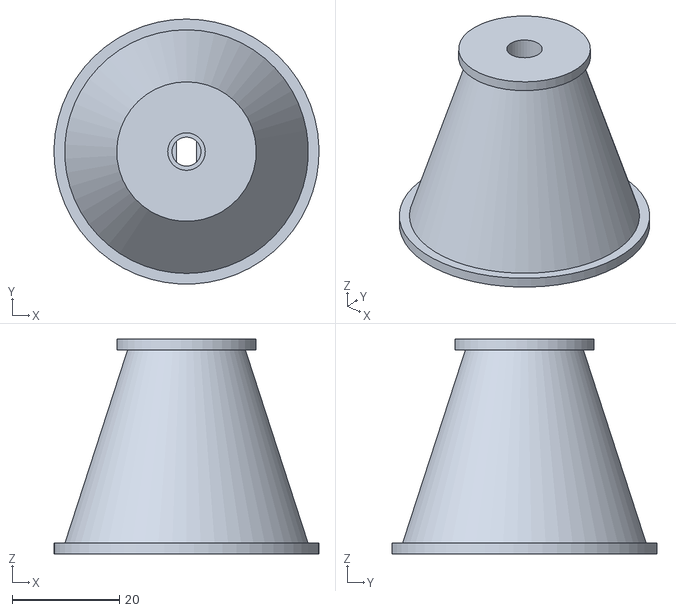
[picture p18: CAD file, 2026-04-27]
docs/CAD_files/2_cone_motor_v2.STL
49.4 x 49.4 x 40.0

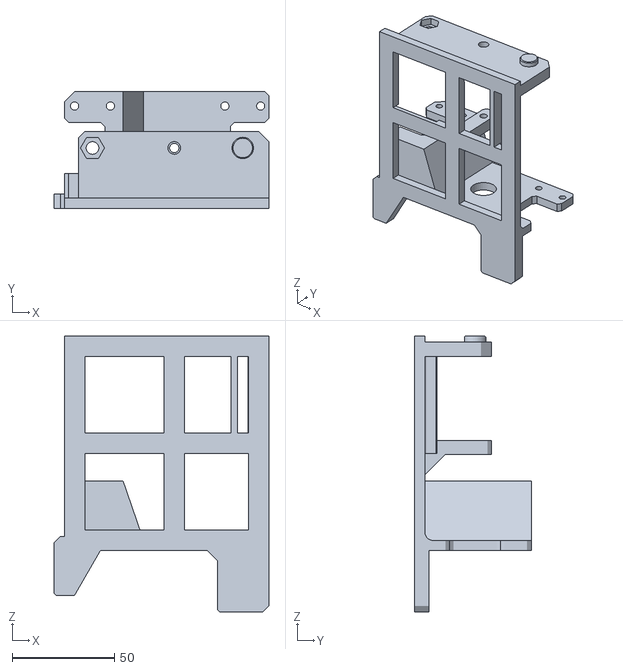
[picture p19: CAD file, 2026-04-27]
docs/CAD_files/1_base_v2.STL
105.0 x 57.0 x 135.0

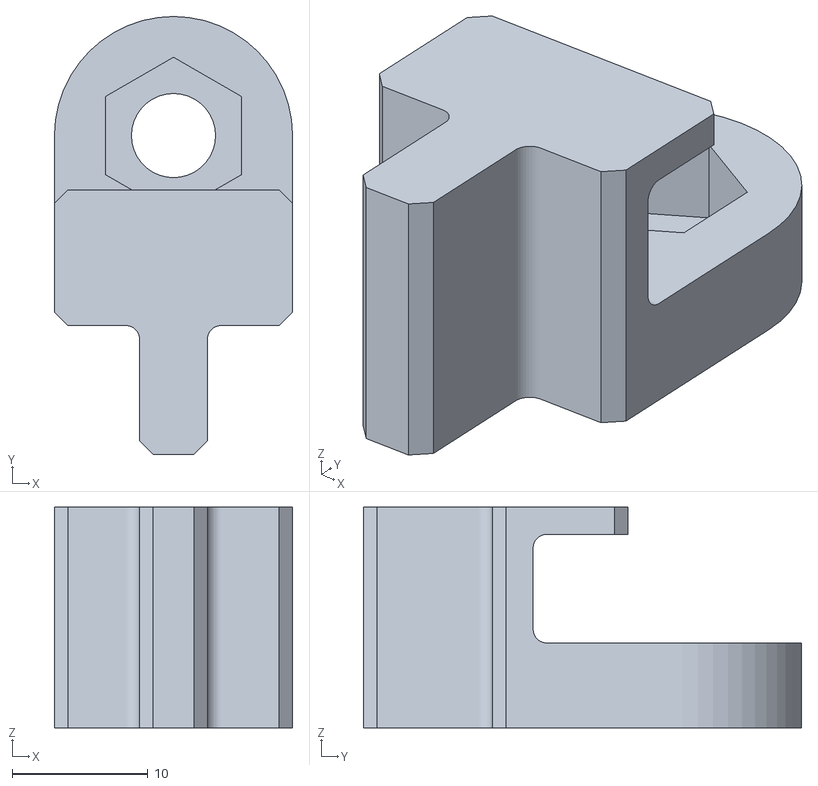
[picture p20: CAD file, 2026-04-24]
docs/CAD_files/7_guia-polia.STL
17.5 x 32.3 x 16.2

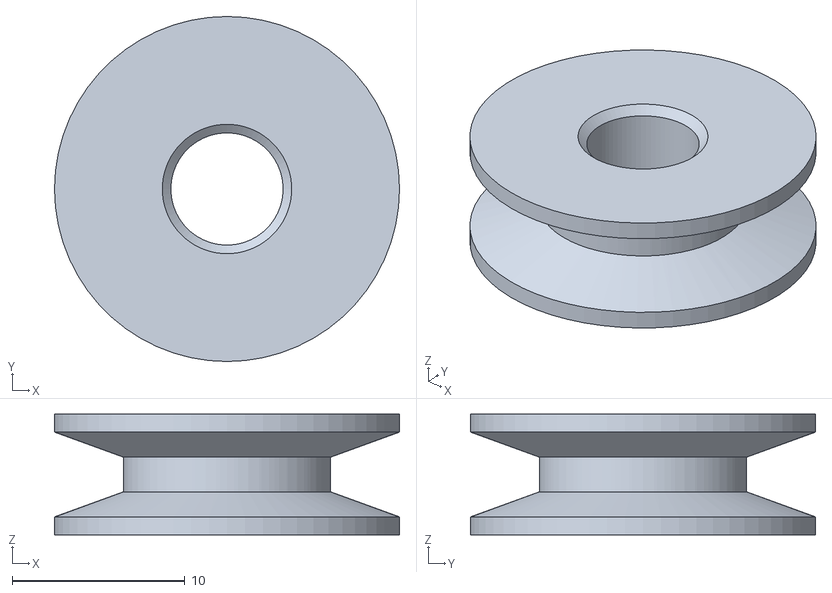
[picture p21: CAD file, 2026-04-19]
docs/CAD_files/5_polia.STL
20.0 x 20.0 x 7.00

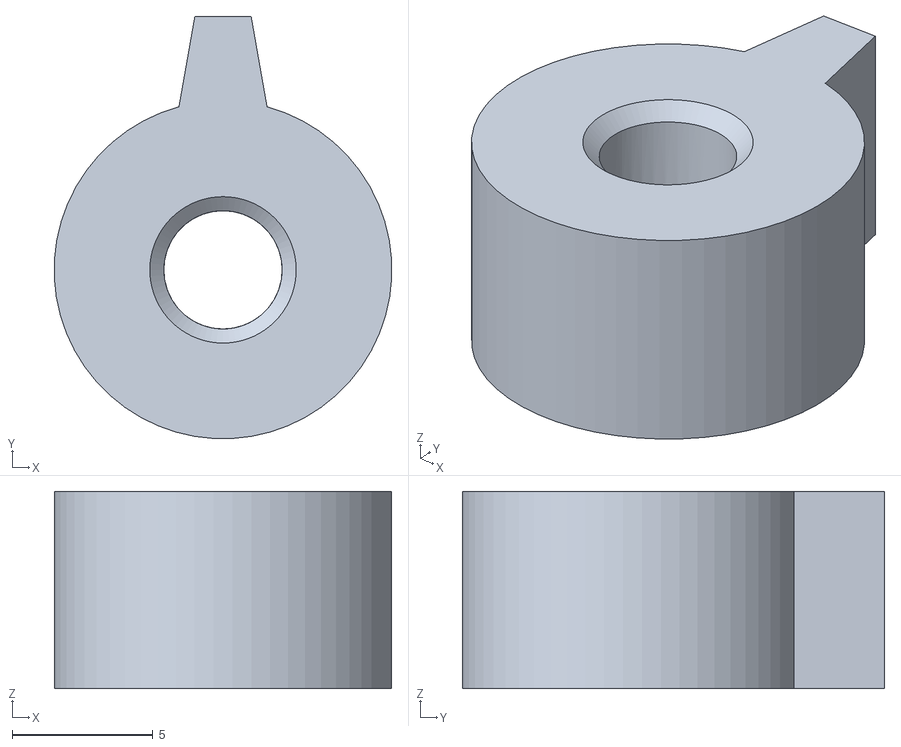
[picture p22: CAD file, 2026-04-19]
docs/CAD_files/4_polia_saida.STL
12.0 x 15.0 x 7.00

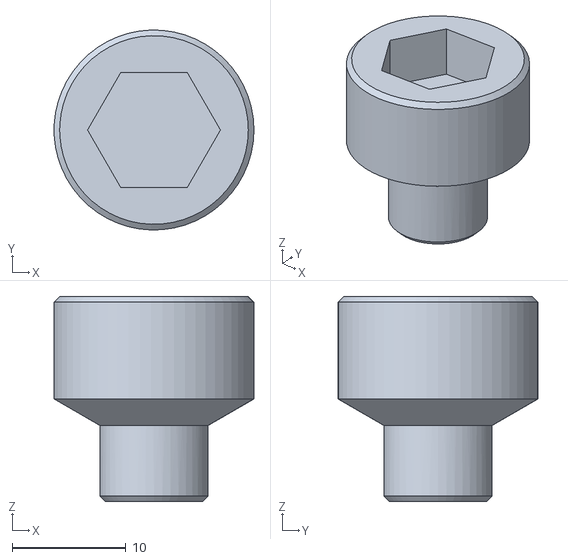
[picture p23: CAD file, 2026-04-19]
docs/CAD_files/6_acoplamento_motor_cvt.STL
17.5 x 17.5 x 18.0

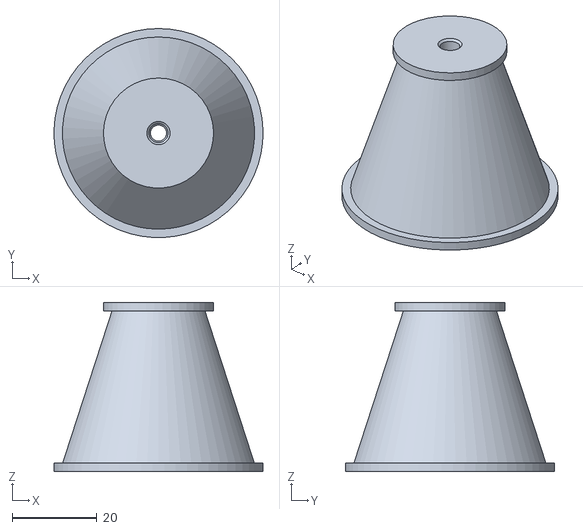
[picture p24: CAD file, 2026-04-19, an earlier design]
docs/CAD_files/3_cone_saida.STL
49.4 x 49.4 x 40.0

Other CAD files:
docs/CAD_files/1_base.STL
docs/CAD_files/2_cone_motor.STL

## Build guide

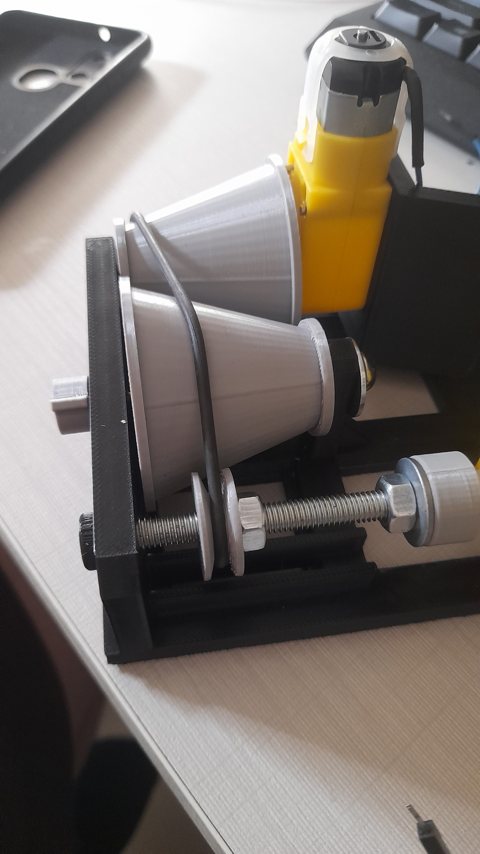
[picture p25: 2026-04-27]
docs/images/montagem_testes/montagem_mec_2.jpg

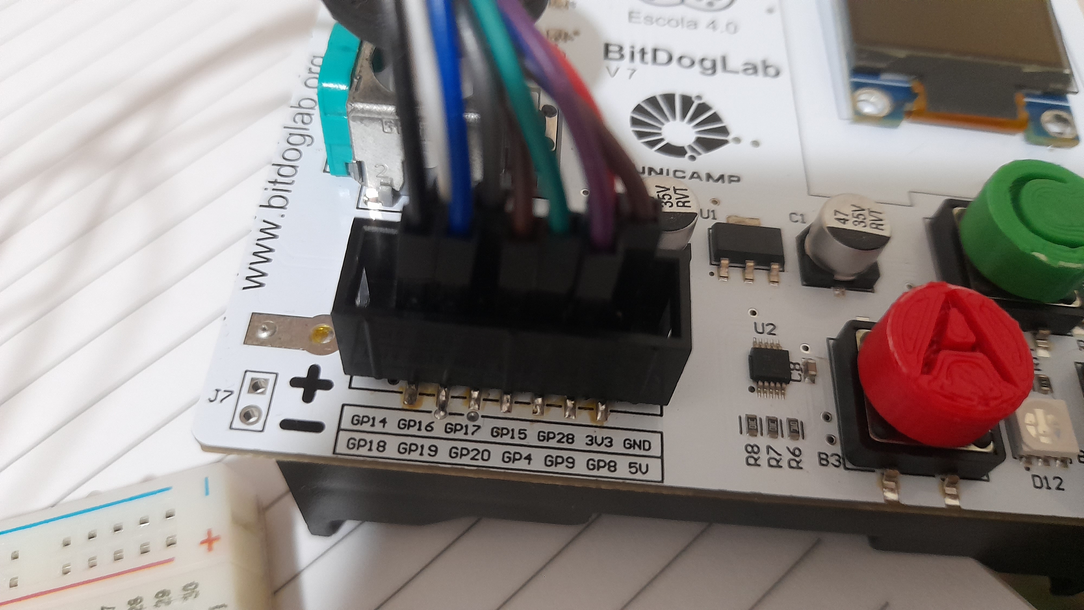
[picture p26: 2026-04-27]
docs/images/montagem_testes/conector_idc_protoboard_1.jpg

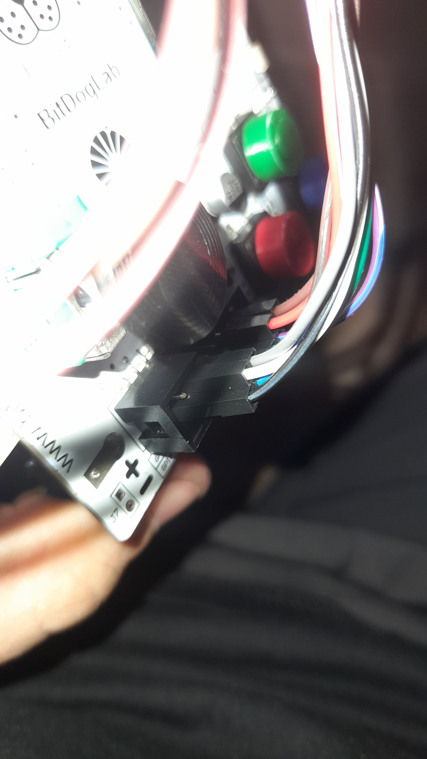
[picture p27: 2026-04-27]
docs/images/montagem_testes/conector_idc_protoboard_6.jpg

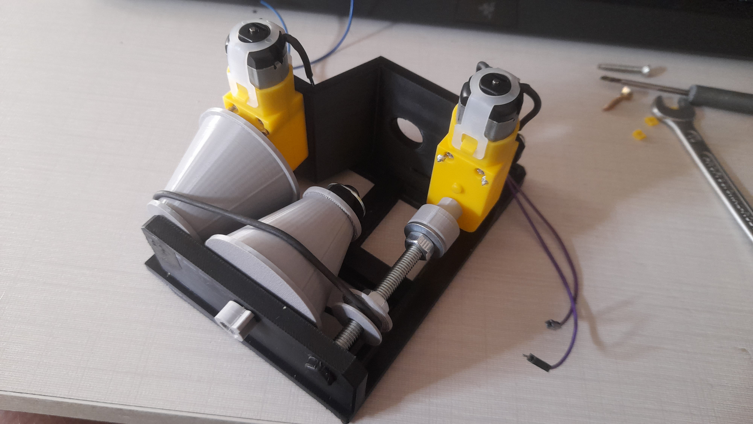
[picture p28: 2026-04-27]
docs/images/montagem_testes/montagem_mec_1.jpg

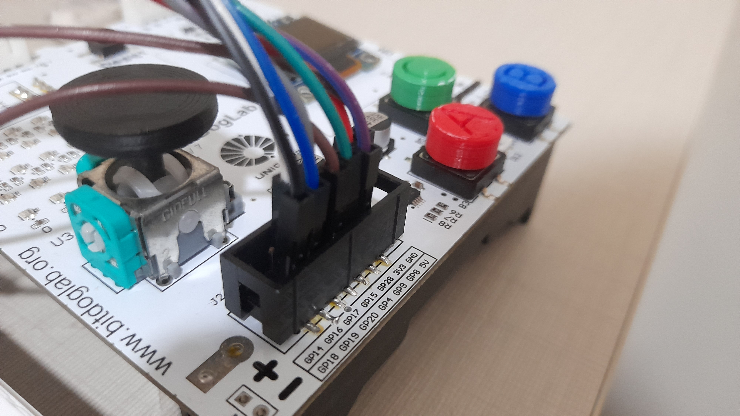
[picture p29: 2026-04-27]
docs/images/montagem_testes/conector_idc_protoboard_3.jpg

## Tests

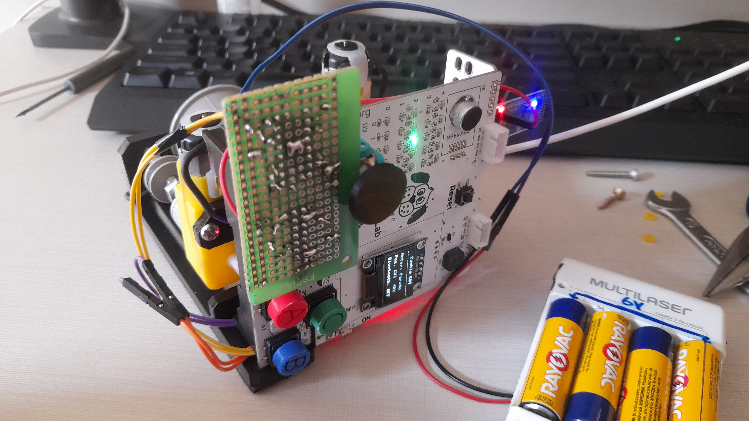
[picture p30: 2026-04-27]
docs/images/montagem_testes/testes_1.jpg

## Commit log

2026-04-12 att gantt_v1.mmd para voltar ao que estava antes
2026-04-18 arquivos para configuracao do hc05
2026-04-18 testes hc05, implementacao do controle sem motor
2026-04-19 monitoramento de conexão bluetooth (on/off) e rampa para parada de emergência ao desconectar
2026-04-19 alt cabeçalho da função printOled
2026-04-19 stl files, pdf3d and deleting backup folder
    [1_base.STL, 2_cone_motor.STL, 3_cone_saida.STL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]
2026-04-22 implementação do controle do câmbio e testes com os motores físicos
2026-04-22 funcionamento assincrono para o motor do cambio cvt
2026-04-24 cad file missing
    [7_guia-polia.STL]
2026-04-27 imagens da montagem, atualização dos .stl, datasheet HC05, imagens do 3D, att comentários da maioria dos .py e removendo scan_i2c.py
    [1_base.STL, 1_base_v2.STL, 2_cone_motor.STL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]
2026-04-27 att readme, datasheets do motor e ponte H, att hc05 config .py para indicar o datasheet na pasta docs
2026-04-27 att readme; novas versões dos diagramas de blocos
2026-04-27 projeto do kicad para a ligação dos componentes e imagem do esquemático
    [ea801_cvt.kicad_pcb, ea801_cvt.kicad_sch]
2026-04-27 att projeto kicad
2026-04-29 alt schematic.png, att projeto kicad, alterando tempo de passo do motor do fuso do câmbio para 2s
2026-04-29 att kicad project
    [ea801_cvt.kicad_sch]
2026-04-29 exc pasta obsoletos no /docs/CAD_files
    [1_base.STL, 2_cone_motor.STL, 3_cone_saida.STL]
